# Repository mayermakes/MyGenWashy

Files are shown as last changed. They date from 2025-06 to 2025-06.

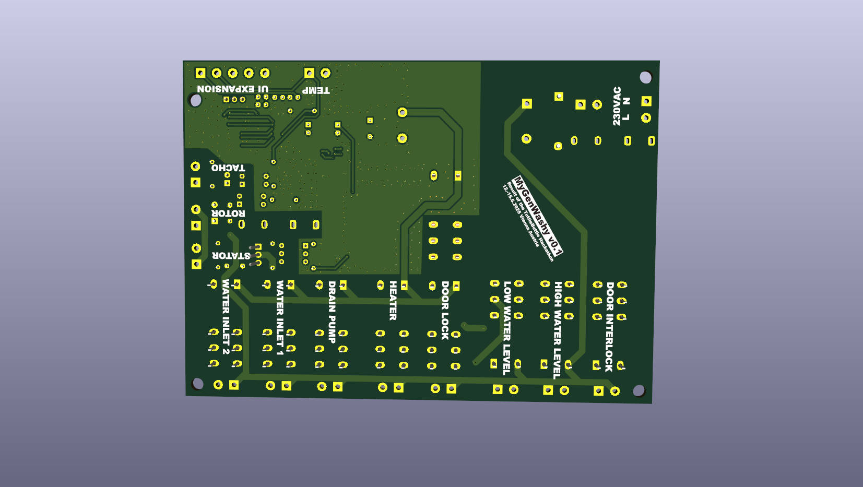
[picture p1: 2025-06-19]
mr_washi_back.png

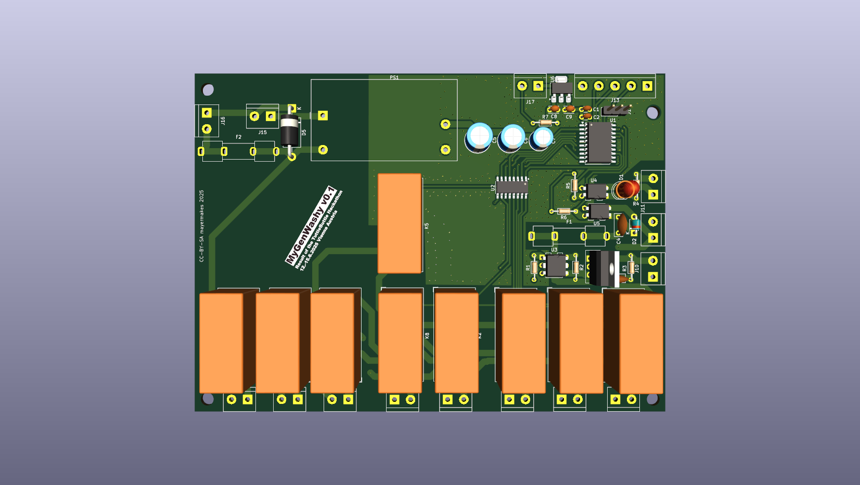
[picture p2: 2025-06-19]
mr_washi.png

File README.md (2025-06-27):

# MyGenWashy
Generic washing Machine Controller - Result of the TuttleButtle Hackathon 2025
held 13.-15.6.2025 in Vienna Austria.

the team got a broken washing machine and set the task to create a generic open source washing machine controler.
the original washing machine and its electronics and a chinese replacement board were partly reverse engineered to understand the functionality.
the team tested their theories on how safety mechanisms and machine parts worked and had to be controlled.
At the end of day two the machine was running a cold wash programm from a dev kit and some homemade electronics controlled via ESP-home.
On day three the learnings and circuits were converted into a kicad design for further testing and software development.

the board is intended to be locally produceable, by hand soldering and easy to repair. We avoided  "special" components for easy component substitution.
Unit cost is not a concerning factor, this is about the availability of a workable design that can be fitted with whatever components are available.

Thanks to Aisler for the Protoype PCBs and Farnell for supporting us with parts!

mr_washi_angled

mr_washi_back_angled

Find the Presentation PDF here:

[Hackathon EN-finial3.pdf](https://github.com/user-attachments/files/20941595/Hackathon.EN-finial3.pdf)

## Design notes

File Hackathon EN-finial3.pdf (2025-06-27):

# MyGenWashy: Modernizing Old

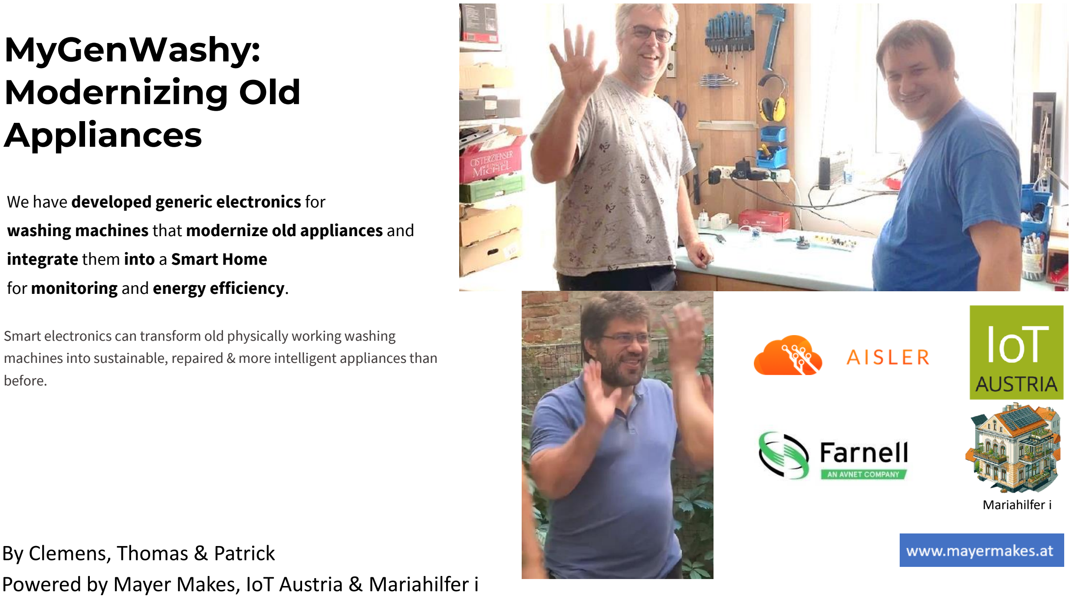
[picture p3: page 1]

# By Clemens, Thomas & Patrick Powered by Mayer Makes, IoT Austria & Mariahilfer i

# Appliances

# Smart electronics can transform old physically working washing machines into sustainable, repaired & more intelligent appliances than

before.

# We have developed generic electronics for

# washing machines that modernize old appliances and

# integrate them into a Smart Home

for monitoring and energy efficiency.

# Mariahilfer i

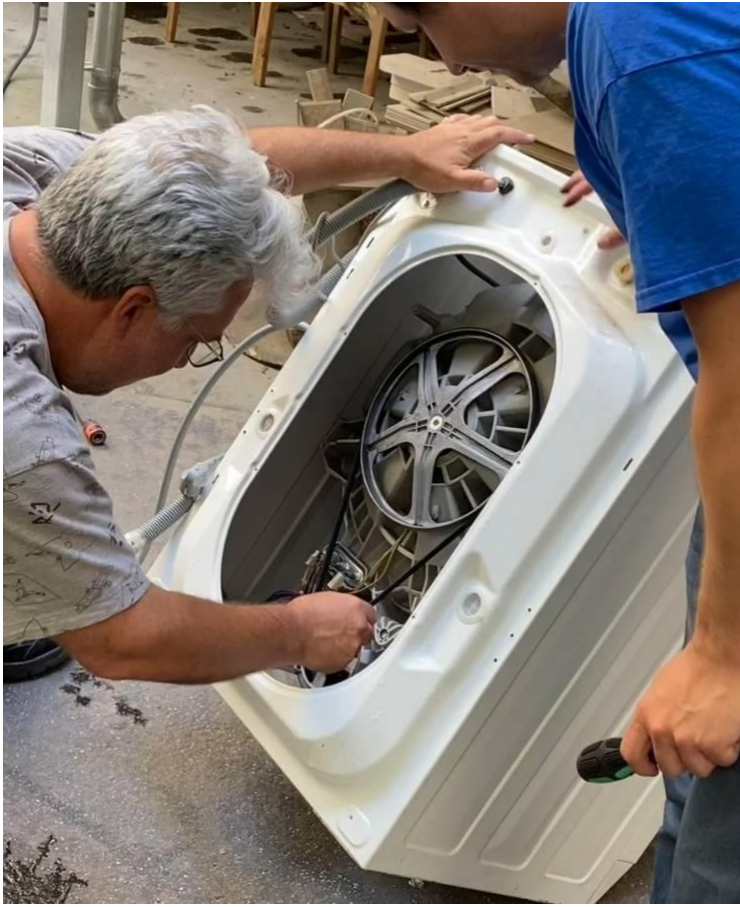
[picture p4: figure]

# Goal of the Hackathon

# Generic electronic components

# Development of a universal control system for washing machines

# Gain knowledge

# Understanding and documenting the components of a

# washing machine

# Smart Home Integration

# Connection to modern home automation systems

# Open Product Pass => http://odpp.at/ (July 2025)

# Create & customize digital documentation for CURRENT products

# Circular economy

# What have we learned?

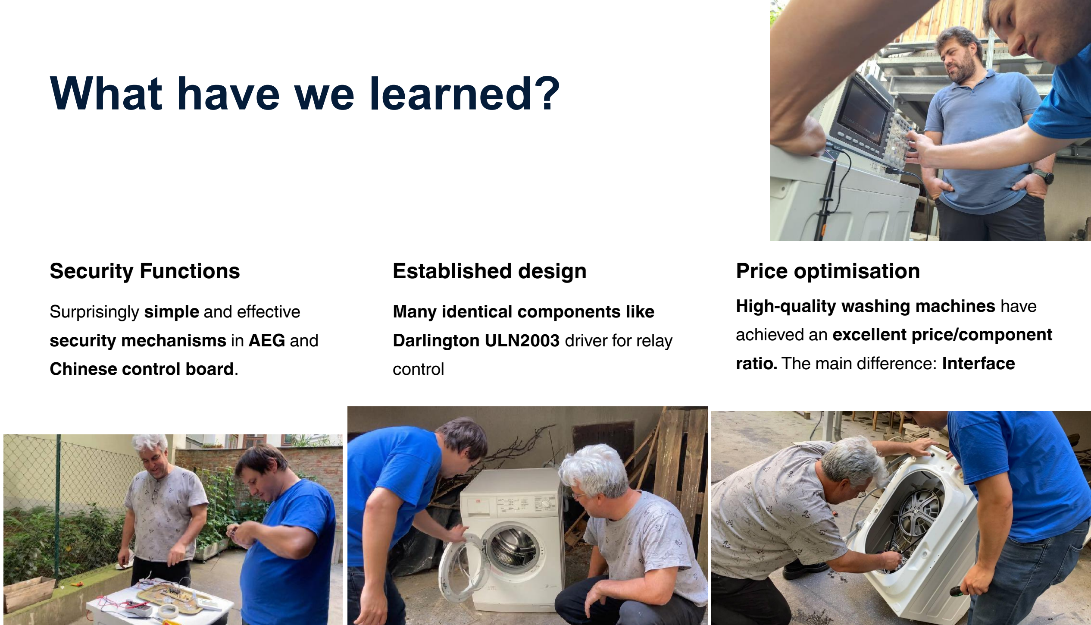
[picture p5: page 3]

# Security Functions

# Surprisingly simple and effective

# security mechanisms in AEG and

Chinese control board.

# Established design

# Many identical components like

# Darlington ULN2003 driver for relay

# control

# Price optimisation

# High-quality washing machines have

# achieved an excellent price/component

# ratio. The main difference: Interface

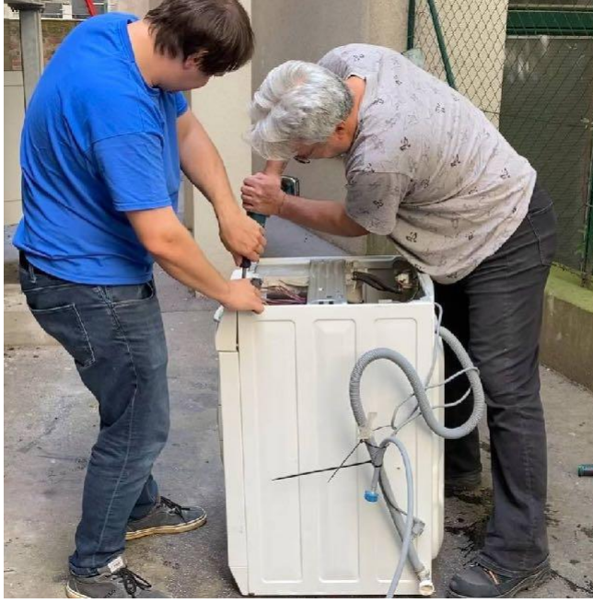
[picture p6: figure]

# Surprising discoveries

# Water level control – by air pressure !?

# Simple air membrane and air pressure => That was unexpected!

# Direct control

# 230V circuit without complex electronics => simplicity is King!

# Security system

Mechanical protection against overflow and overheating => Safety first – also on Chinese generic boards!

# Conclusions

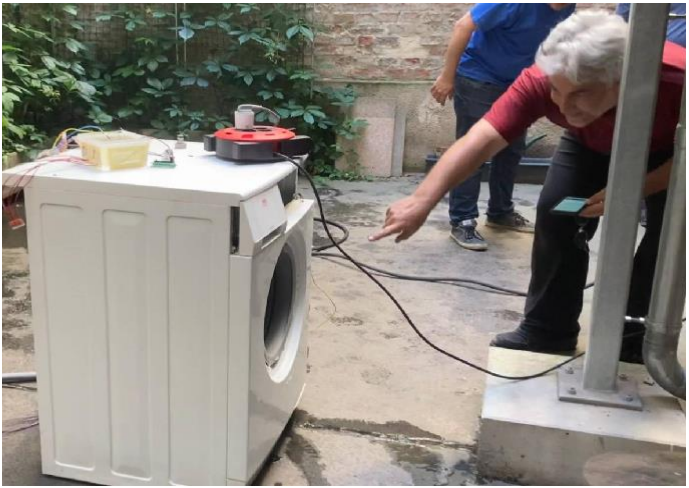
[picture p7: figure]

# Sophisticated technology

# The operating principle of a

# washing machine is fully

# developed and optimized

# Circular Economy

# High-quality machines can

# simply continue to be

# operated with new

# electronics. QED

# Sustainability: Refabrication, Pimp

# Replacing the electronics of an old washing machine with a

# generic one that has more energy-saving functions and is easier

# to control. This saves resources and reduces electronic waste!

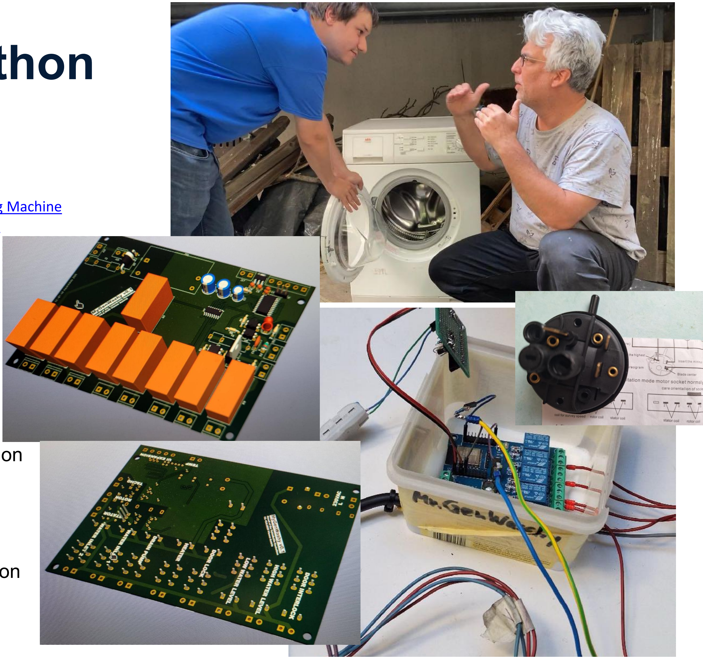
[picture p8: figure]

# Results of the Hackathon

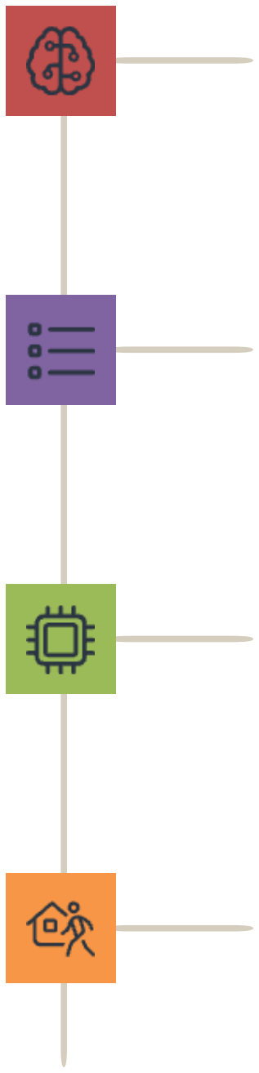
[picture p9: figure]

# Schematic for circuit v1/3

# Component list v1/3

# Complete component documentation

# Board v1/3

# PCB design for the MadWashyMax Edition

# Smart Home Integration

# GitHub - mayermakes/MyGenWashy: Generic washing Machine

Controller - Result of the TuttleButtle Hackathon 2025 (https://github.com/mayermakes/MyGenWashy)

# PCB design for the MadWashyMax Edition

# (intermediate Version here – will be

# updated once PCB Board v1 is here …)

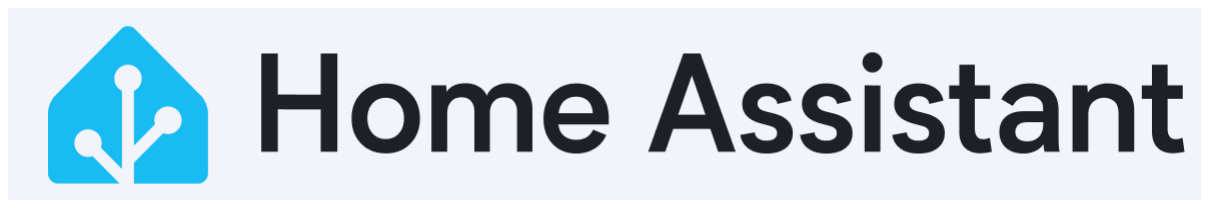
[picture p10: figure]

esphome:
name: mygenwashy-v2
friendly_name: MyGenWashy-v2

esp32:

board: esp32dev

framework:
type: arduino

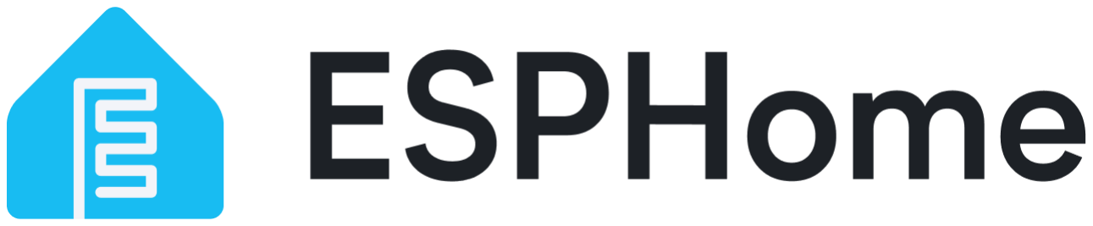
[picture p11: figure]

logger:
level: VERBOSE

output:
- platform: gpio

pin: GPIO32

id: relay_pin_1_relay_cold_water_valve
- platform: gpio

pin: GPIO33

id: relay_pin_2_relay_pump
- platform: gpio

pin: GPIO25

id: relay_pin_3_relay_montor_stator
- platform: gpio

pin: GPIO26

id: relay_pin_4_relay_montor_aktor
- platform: ledc #PWM Motor Speed

pin: GPIO27

frequency: 1000 Hz
id: pwm_motor

switch:

- platform: output
id: switch_relay_cold_water_valve

name: "R1 - Kaltwasserventil"

icon: mdi:Water
output: relay_pin_1_relay_cold_water_valve

restore_mode: RESTORE_DEFAULT_OFF

- platform: output
id: switch_relay_relay_pump

name: "R2 - Wasser abpumpen" icon: mdi:Pump
output: relay_pin_2_relay_pump
- platform: output
id: switch_relay_montor_stator name: "R3 - Motor Stator"
icon: mdi:Motor

output: relay_pin_3_relay_montor_stator

- platform: output
id: switch_relay_pin_4_relay_montor_aktor

name: "R4 - Motor Aktor"
icon: mdi:MotorAktor

output: relay_pin_4_relay_montor_aktor fan: #Washing Machine Rince Speed

- platform: speed
output: pwm_motor
name: "Motor Rotor Speed 3" icon: mdi:fan-speed-3
- platform: speed

output: pwm_motor
name: "Motor Stator Speed 2" icon: mdi:fan-speed-2

sensor:
- platform: ntc #NTC

sensor: resistance_sensor
calibration: #datasheet - or calkibrated - user instrcutions - MrWashyBalls #- 10.0kOhm -> 25°C

#- 27.219kOhm -> 0°C

#- 14.674kOhm -> 15°C

b_constant: 3950
reference_temperature: 25°C

reference_resistance: 10kOhm

name: "Water Temperature (NTC)" icon: mdi:thermometer-snowflake

- platform: resistance

id: resistance_sensor

sensor: source_sensor
configuration: DOWNSTREAM
resistor: 5 kOhm #Messen

name: Resistance Sensor

- platform: adc
id: source_sensor
pin: GPIO35

update_interval: 60s

- platform: gpio

pin:

number: GPIO34

mode: INPUT
inverted: false

name: "Umdrehungssignal"
filters:
- delayed_on: 10ms
- delayed_off: 10ms
icon: mdi:counter

# ESPHome & Home Assist

# ESPHome - Home Assistant (https://www.home-assistant.io/integrations/esphome)

# mygenwashy-v1.yaml

# remarks: Motor driver & NTC calibration will follow in

v2

# OnPrem Smart Home

# Post-apocalyptic SmartHome

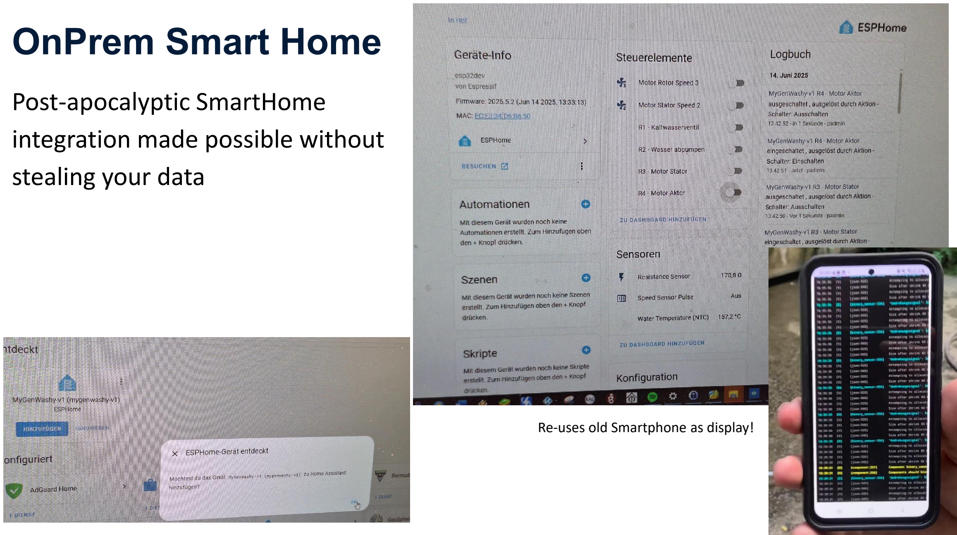
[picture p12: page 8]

# integration made possible without stealing your data

# Re-uses old Smartphone as display!

# Minimal Arch / i2c Bus / OnPrem Smart Home

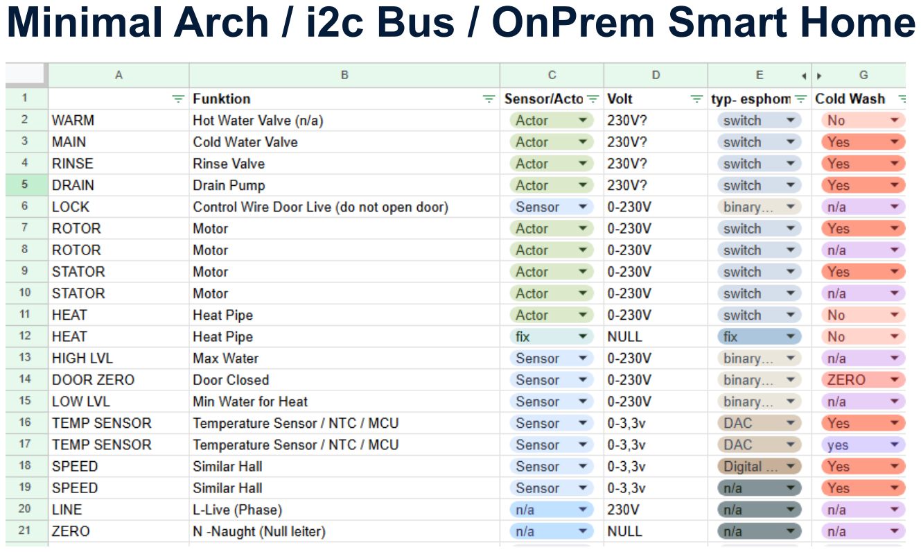
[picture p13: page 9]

# Modified MadWashyMax

# Hardware modification

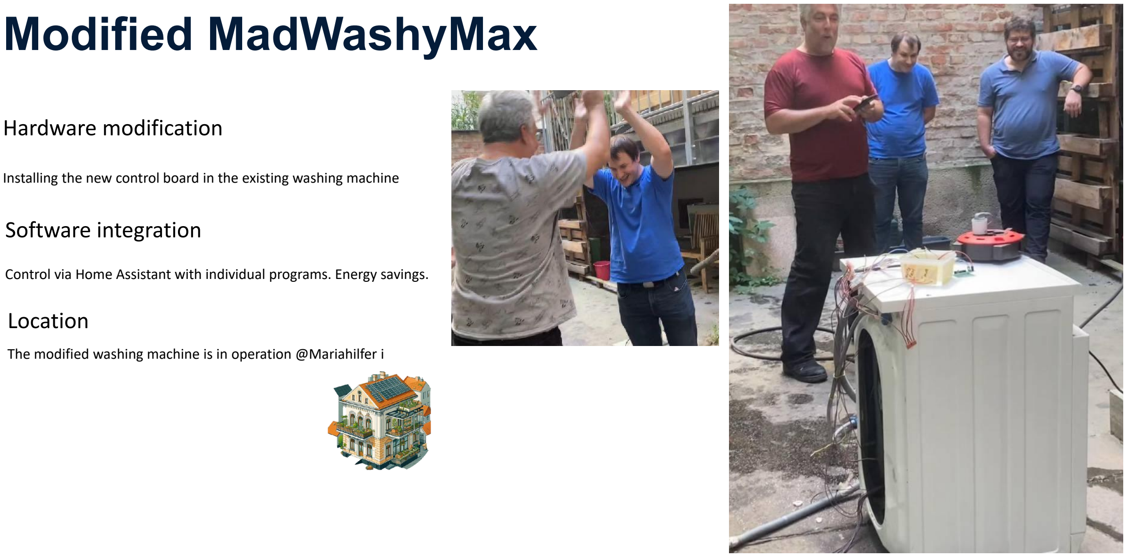
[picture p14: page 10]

# Installing the new control board in the existing washing machine

# Software integration

Control via Home Assistant with individual programs. Energy savings.

# Location

# The modified washing machine is in operation @Mariahilfer i

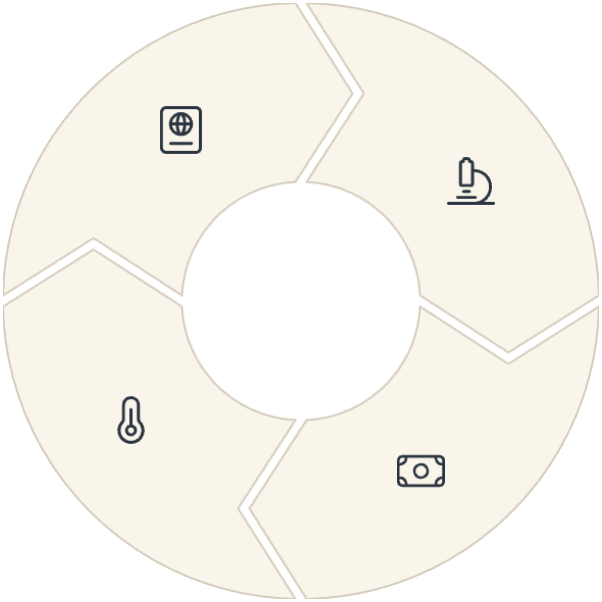
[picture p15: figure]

# Open Digital Product Pass – ODPP

# Examples of 4 household

# appliances incl. MadWashyMax =>

# in July check http://odpp.at/

# Washing quality monitoring

# StartUp idea for monitoring cleaning

# performance

# EnergyMate

# Control with dynamic electricity

# prices (StartUp)

# Energy-optimized water heating

# Real-time control for maximum

# efficiency

# Follow-Ups & Spin-Offs

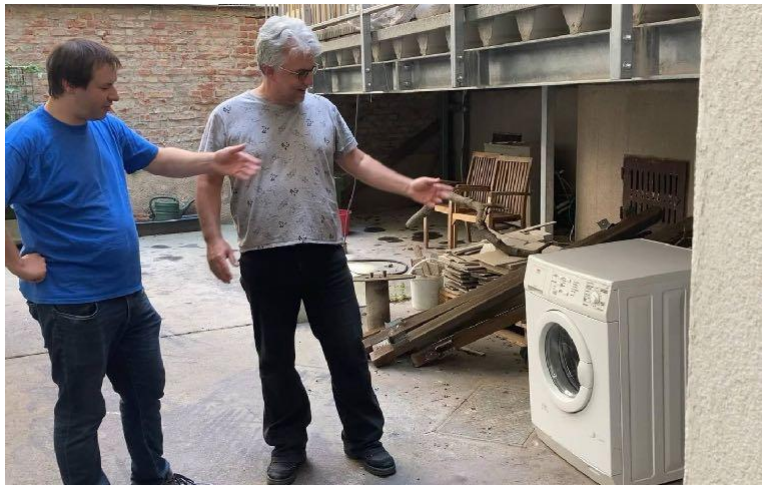
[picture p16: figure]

# Future vision

# Promoting sustainability

# Extend the service life of household appliances.Washing

machine => e-toothbrush => washing machine .... etc...

# Build a community => http://odpp.at/ (July)

Share knowledge and experiences.

# Driving innovation forward

# Develop new applications for existing technology. Which can be

# used TODAY by anyone!

# Our project shows how we can use open source technology to

# reduce e-waste and create new business models at the same time

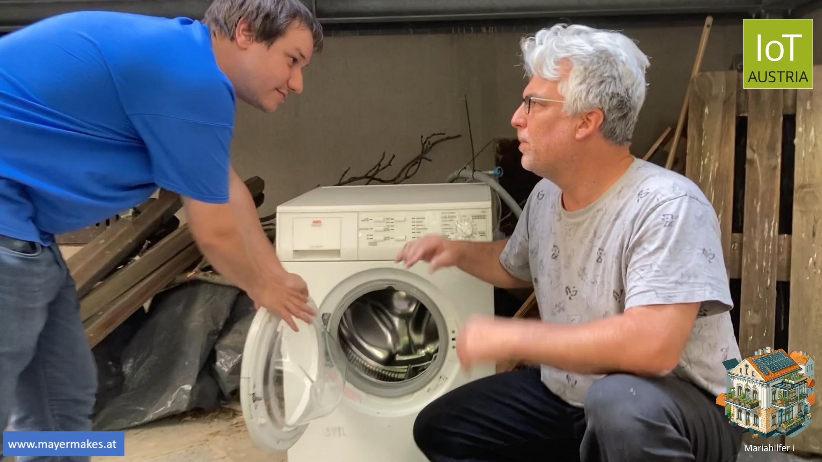
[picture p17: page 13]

# Mariahilfer i

# Tadaaa!

# Water

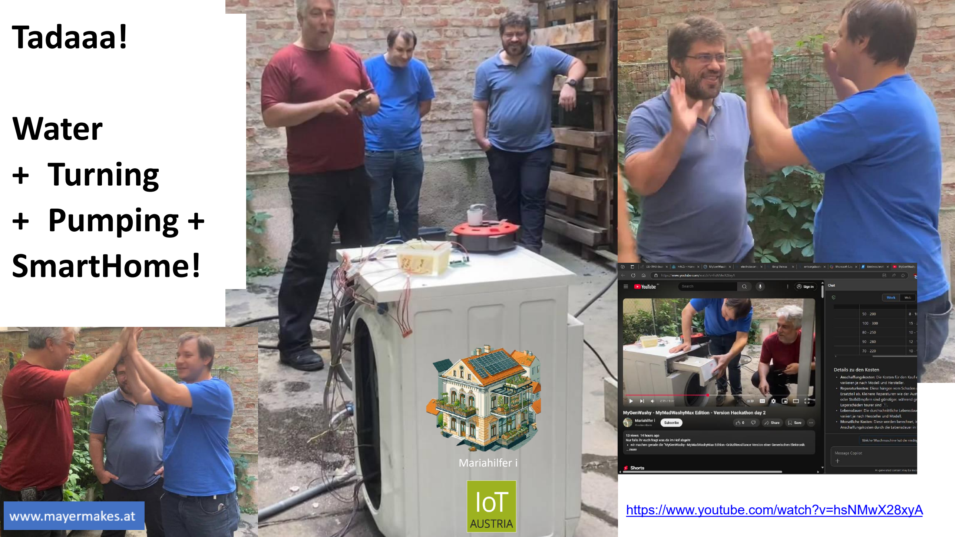
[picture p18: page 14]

# + Turning + Pumping + SmartHome!

# https://www.youtube.com/watch?v=hsNMwX28xyA

# Mariahilfer i

# Clemens Mayer

MAYER MAKES e.U.

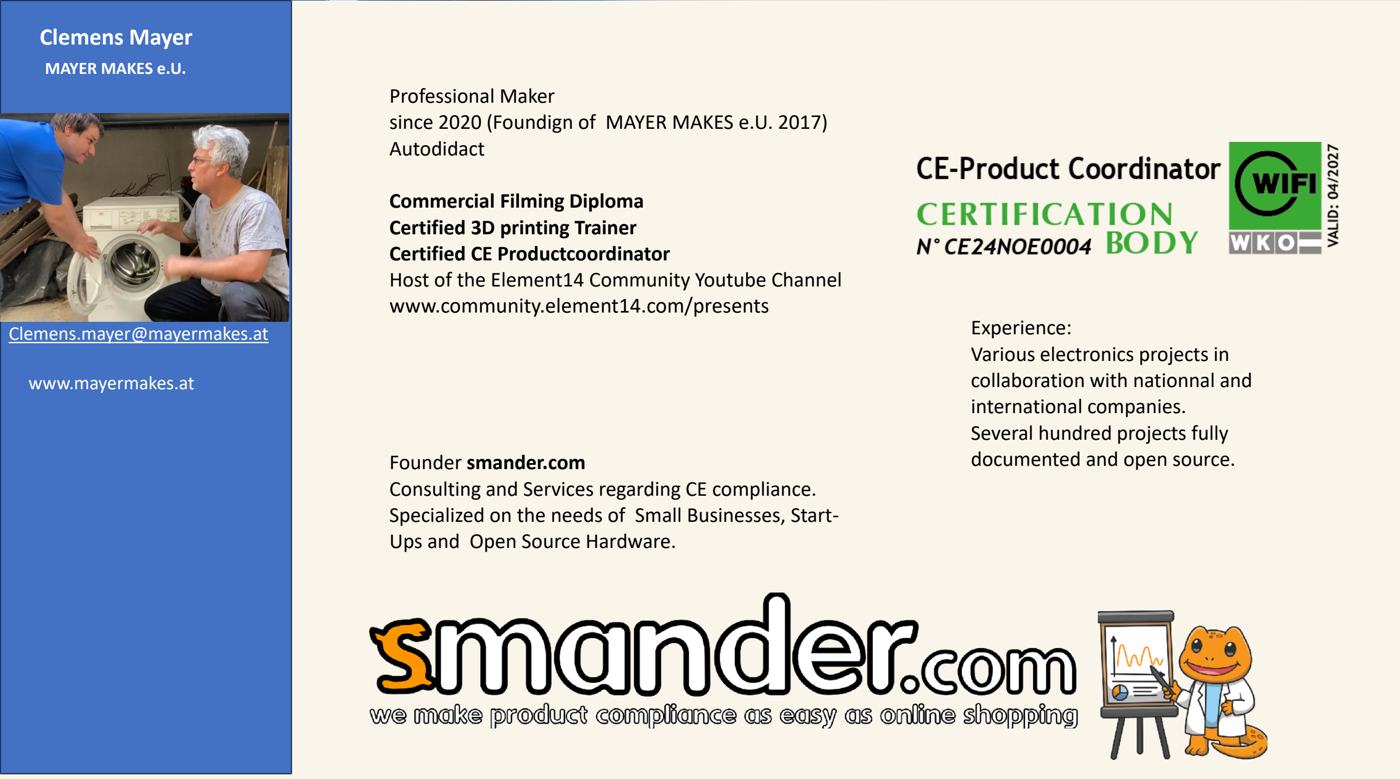
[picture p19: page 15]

# Clemens.mayer@mayermakes.at

# www.mayermakes.at

# Professional Maker since 2020 (Foundign of MAYER MAKES e.U. 2017) Autodidact

# Commercial Filming Diploma Certified 3D printing Trainer Certified CE Productcoordinator Host of the Element14 Community Youtube Channel

# www.community.element14.com/presents

# Founder smander.com

Consulting and Services regarding CE compliance.

# Specialized on the needs of Small Businesses, Start-

Ups and Open Source Hardware.

# Experience: Various electronics projects in collaboration with nationnal and

international companies.

# Several hundred projects fully

documented and open source.

DI Patrick Ch. AWART | Ausbildung:
| • Master TU Wien / Technische Informatik 2001 • Data Science / Hopkins Universität 2017

# Kernkompetenzen:

# - Innovation Lead / Guide for Digital Transformation - KI Experte & Data Scientist - Wissensmanagement - Complex System Assessment / Evaluation

# - AI Roadmap & Strategiefindung

- Smart Product Use Case Entwicklung, Bewertung,

# Spezifizierung und Umsetzungsverantwortung

# - Python / Node js / IoT / … / (No-)SQL / Elastic Stack / diverse Programmier & Abfragesprachen von C über

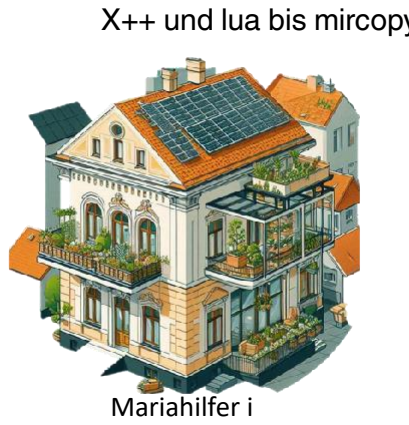
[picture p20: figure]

X++ und lua bis mircopython der letzten 35 Jahre.

# Fortbildung, Kurse & Zertifizierungen:

# - Google Advanced AI Solutions 2019

# - Azure ML 2018

# - Scrum Master 2018

# - Zertifizierter Innovationsmanager 2008

# - Microsoft Certified Professional 2013

# Projekte / Erfahrung:

# Maßgebliche fachliche Leitung von Digitalen

Transformationsprojekten in den Branchen SmartCity,

# eGoverment, Public Health & Krisenmanagement Systeme -

seit 25 Jahren.

# Principal Solution Architect

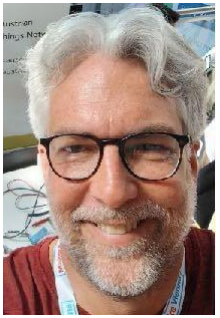
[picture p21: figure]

# p@awart.net

+43 664 88 55 13 77

# Sprachen: D, E, F

# stolzer Vater von 2 Kindern (Bea hat mit 4

# Jahren löten gelernt)

# Hobby: Hiking/Volleyball/ MTB

# Kreislaufwirtschaftliche Entwicklung im

# Bestand Energiegemeinschaften &

# Lastprofil-optimierung

# Co-Gründer Mariahilfer i Nov 2024 360°

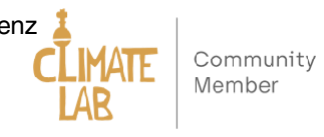
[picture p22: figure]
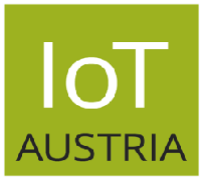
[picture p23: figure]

# Gräzl-Resilienz

# - Von der Vision über die Prozess- & Anforderungsanalyse bis hin zum Go Live

# - Strategieentwicklung und Umsetzung

# - DPP / Digitaler Produktpass - ODPP / Offener DPP

# - Kintsugi Repair Cafe - (u.a.Wohn Interieur)

# - KI-Wissensmanagement Mariahilfer i

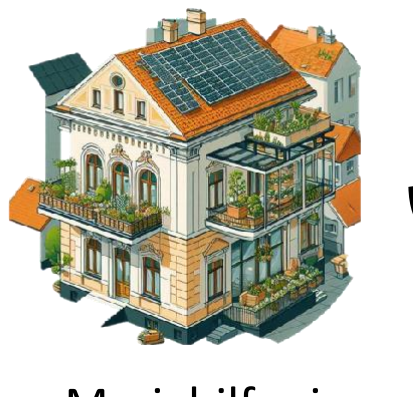
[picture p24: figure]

# JOIN US for v2, v3 & StartUps!

# Get in touch and participate in our future projects advancing open source and reusability

# Patrick Awart

# Thomas Losert

# Clemens Mayer

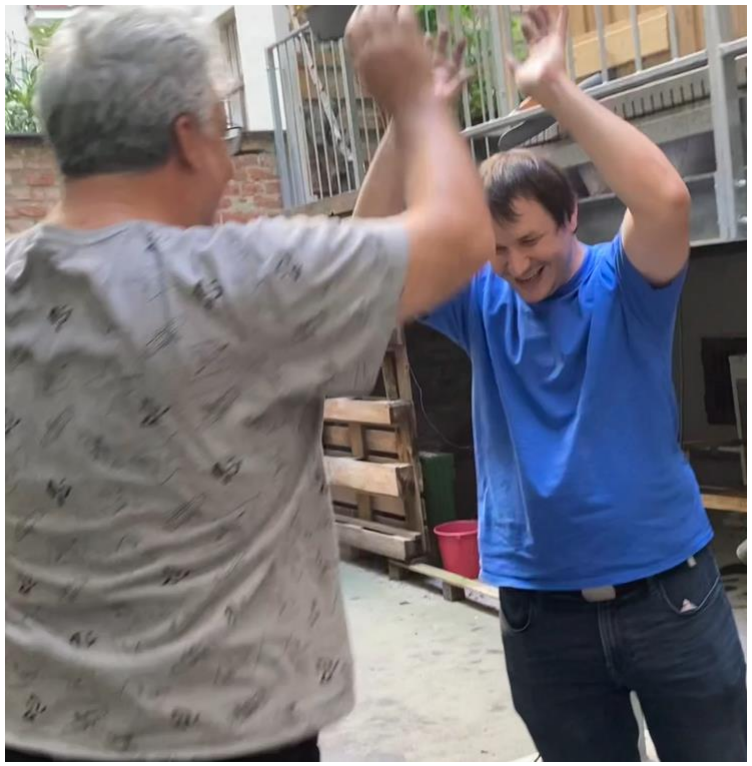
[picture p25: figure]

# Open Digital Product Pass => http://odpp.at/ (July 2025) contribute@odpp.at

# Mariahilfer i

# MANY Thx go to:

Albert (pixs, Transport, Vids, PPT !), Johanna (Washing machine!), Birgit (UX Feedback & Requirements Feedback),

Boots Owen (Many Many Useful tips!!!) check out: https://youtu.be/f2Fo3-SVfDs Farnell – components Aisler – PC Board Infineon – AI Boards Gorenje – CircThread Inspiration for ODPP! D. (crimping!) Kintsugi Repair Café (Space!) CargoBike! Gemma, CoPilot, etc. Cool AI Pictures raising the Adrenalin Levels! Elektra and Nescafe Coffee machine RuSZ: David & Dagmar – Aligning Elektro Kuchling: Feedback of current sales practice & Inspiration on ReUse Ideas Generic (!!!) Water Adapter from WaterFront lying around – you saved us! !!! Let's keep up the great Work & Vibes!!!

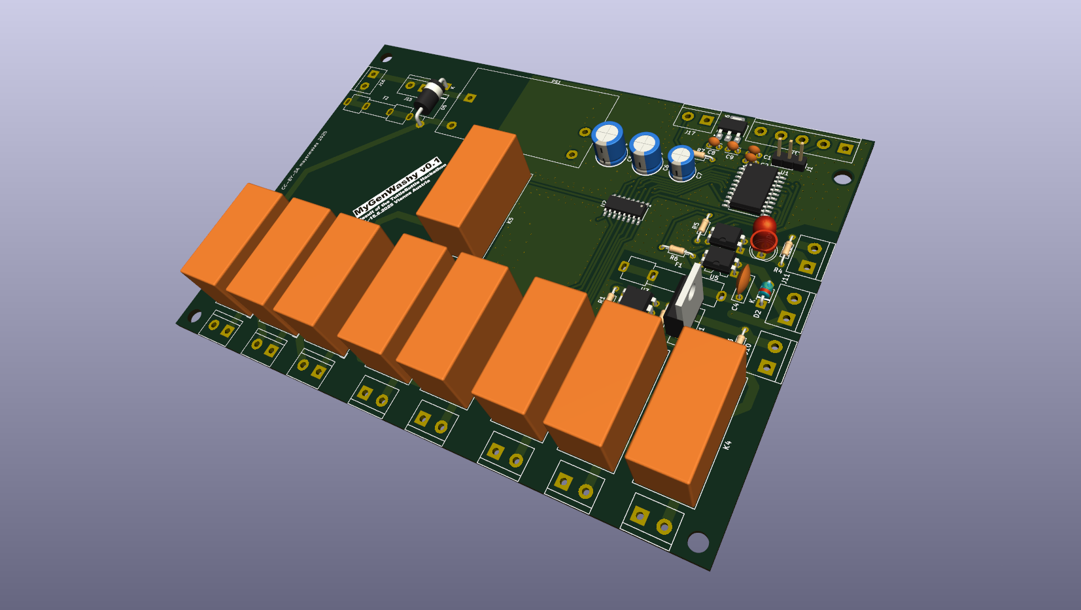
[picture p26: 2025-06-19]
mr_washi_angled.png

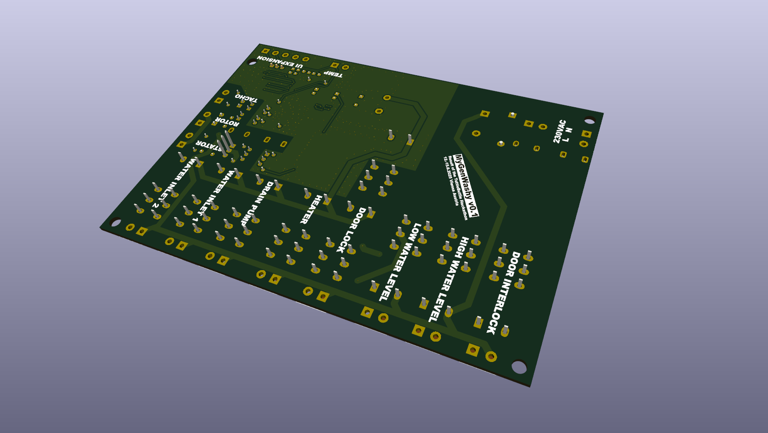
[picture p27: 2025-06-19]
mr_washi_back_angled.png

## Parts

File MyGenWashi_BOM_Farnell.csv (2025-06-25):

Nr. | Best.-Nr. | RoHS-konform? | Ihre Bestellnummer | Hinweise | Menge | Hersteller-Teilenr. | Herstellername | Hersteller / Beschreibung | Verfügbarkeit | Stückpreis (&euro;) | Positionspreis (&euro;) | Rabattpreis (&euro;)
1 | 3765485 | RoHS: YES / PHTHALATE: YES |  |  | 6.0 | PS2562L1-1-A | RENESAS | RENESAS Optokoppler, 1 Kanal, DIP, Oberflächenmontage, 4 Pin(s), 80 mA, 5 kV, 200 % | 671 | 0.9710 | 5.83
2 | 8767068 | RoHS: YES / PHTHALATE: YES |  |  | 5.0 | ECA1AAM331X | PANASONIC | PANASONIC Elektrolytkondensator, 330 µF, 10 V, ± 20%, Radial bedrahtet, 2000 Stunden bei 85°C, Polarisiert | 1905 | 0.1130 | 0.57
3 | 1459143 | RoHS: Y-EX / PHTHALATE: YES |  |  | 5.0 | MUR2100EG | ONSEMI | ONSEMI Diode mit kurzer/ultrakurzer Erholzeit, 1 kV, 2 A, Einfach, 2.2 V, 75 ns, 35 A | 6522 | 0.4570 | 2.29
4 | 3406865 | RoHS: YES / PHTHALATE: YES |  |  | 10.0 | RTD14730 | SCHRACK - TE CONNECTIVITY | SCHRACK - TE CONNECTIVITY Leistungsrelais, SPDT, 230 VAC, 16 A, RT1, Durchsteckmontage, Monostabil | 532 | 6.5700 | 65.70
5 | 3705262 | RoHS: YES / PHTHALATE: YES |  |  | 40.0 | 1755736 | PHOENIX CONTACT | PHOENIX CONTACT STIFTLEISTE, VERT 5.08MM 2POL. | 3030 | 0.9610 | 38.44
6 | 3705389 | RoHS: Y-EX / PHTHALATE: YES |  |  | 2.0 | 1757048 | PHOENIX CONTACT | PHOENIX CONTACT Steckbare Reihenklemme, 5.08 mm, 5 -polig, 24 AWG, 12 AWG, 2.5 mm², Schraubanschluss | 1234 | 5.7600 | 11.52
7 | 3705201 | RoHS: YES / PHTHALATE: YES |  |  | 2.0 | 1757271 | PHOENIX CONTACT | PHOENIX CONTACT Reihenklemme, abgewinkelt, Stiftleiste, 5.08 mm, 5 -polig, 12 A, 250 V | 1065 | 1.8900 | 3.78
8 | 1581137 | RoHS: YES / PHTHALATE: YES |  |  | 5.0 | MCL053MD | MULTICOMP PRO | MULTICOMP PRO LED, Rot, Durchsteckmontage, T-1 3/4 (5mm), 20 mA, 2 V, 625 nm | 34709 | 0.1260 | 0.63
9 | 3772379 | RoHS: YES / PHTHALATE: YES |  |  | 10.0 | FG18X5R1E106MRT00 | TDK | TDK Keramikvielschichtkondensator, 10 µF, 25 V, ± 20%, PC-Pin, X5R, 2.5 mm | 489 | 0.2650 | 2.65
10 | 3289391 | RoHS: YES / PHTHALATE: YES |  |  | 10.0 | K104Z15Y5VE5TH5 | VISHAY | VISHAY Keramikvielschichtkondensator, 0.1 µF, 25 V, -20%, +80%, Radial bedrahtet, Y5V, 5 mm | 294 Verfügbar | bis der Lagerbestand erschöpft ist. | 0.1060 | 1.06
11 | 4143903 | RoHS: YES / PHTHALATE: YES |  |  | 5.0 | FG23C0G2W104JNT00 | TDK | TDK Keramikvielschichtkondensator, 0.1 µF, 450 V, ± 5%, PC-Pin, C0G / NP0, 5 mm | 386 | 3.0000 | 15.00
12 | 2534925 | RoHS: YES / PHTHALATE: YES |  |  | 10.0 | C981U103MYVDAAWL45 | KEMET | KEMET Funkentstörkondensator (Keramik), Scheibenkondensator, 0.01 µF, ± 20%, X1 / Y2, 400 V, 250 V | 5900 Verfügbar | bis der Lagerbestand erschöpft ist. | 0.3340 | 3.34
13 | 1471017 | RoHS: YES / PHTHALATE: YES |  |  | 3.0 | MOC3020-M | ONSEMI | ONSEMI Optokoppler, Triac-Ausgang, DIP, 6 Pin(s), 5.3 kV, Momentwert, 400 V, MOC301XM & MOC302XM | 4446 | 0.7160 | 2.15
14 | 1578404 | RoHS: YES / PHTHALATE: YES |  |  | 5.0 | MCP1825S-3302E/DB | MICROCHIP | MICROCHIP LDO-Festspannungsregler, 2.1V bis 6V, 210mV Dropout, 3.3Vout, 500mAout, SOT-223-3 | 50652 | 0.6290 | 3.15
15 | 1653491 | RoHS: YES / PHTHALATE: YES |  |  | 4.0 | BTB16-600BWRG | STMICROELECTRONICS | STMICROELECTRONICS Triac, 600 V, 16 A, TO-220AB, 1.3 V, 160 A, 50 mA | 1236 | 1.2800 | 5.12
16 | 3619410 | RoHS: YES / PHTHALATE: YES |  |  | 5.0 | MP006456 | MULTICOMP PRO | MULTICOMP PRO Widerstand für Durchsteckmontage, 47 kohm, 1 W, ± 2%, Axial bedrahtet, 500 V | 1545 | 0.2590 | 1.30
17 | 2815498 | RoHS: YES / PHTHALATE: YES |  |  | 2.0 | IRM-10-5 | MEAN WELL | MEAN WELL AC/DC-Netzteil für Leiterplattenmontage, ITE, 1 Ausgang, 10 W, 5 VDC, 2 A | 64 | 10.7400 | 21.48
18 | 2325629 | RoHS: YES / PHTHALATE: YES |  |  | 20.0 | 1-1415899-9 | SCHRACK - TE CONNECTIVITY | SCHRACK - TE CONNECTIVITY Universelles Leistungsrelais, Baureihe RZ, monostabil, SPDT, 5V DC, 16A | 3485 | 1.8600 | 37.20
19 | 1217315 | RoHS: YES / PHTHALATE: YES |  |  | 40.0 | MC 100-50802 | LUMBERG | LUMBERG Steckbare Reihenklemme, 5.08 mm, 2 -polig, 24 AWG, 14 AWG, Schraubanschluss | 1780 Verfügbar | bis der Lagerbestand erschöpft ist. | 0.9440 | 37.76
20 | 9452192 | RoHS: YES / PHTHALATE: YES |  |  | 5.0 | MCUMR16V106M4X5 | MULTICOMP PRO | MULTICOMP PRO Elektrolytkondensator, 10 µF, 16 V, ± 20%, Radial bedrahtet, 1000 Stunden bei 85°C, Polarisiert | 68408 | 0.1040 | 0.52
21 | 1902919 | RoHS: YES / PHTHALATE: YES |  |  | 5.0 | MCRH50V104M5X11 | MULTICOMP PRO | MULTICOMP PRO Elektrolytkondensator, 0.1 µF, 50 V, ± 20%, Radial bedrahtet, 2000 Stunden bei 105°C, Polarisiert | 302 | 0.0788 | 0.39
22 | 9338055 | RoHS: YES / PHTHALATE: YES |  |  | 5.0 | MCF 2W 1K | MULTICOMP PRO | MULTICOMP PRO KOHLESCHICHTWIDERSTAND 1K 5% 2W AXIAL | 95811 | 0.1540 | 0.77
23 | 9338705 | RoHS: YES / PHTHALATE: YES |  |  | 5.0 | MCF 0.5W 330R | MULTICOMP PRO | MULTICOMP PRO Widerstand für Durchsteckmontage, 330 ohm, MCF Series, 500 mW, ± 5%, Axial bedrahtet, 350 V | 10903 | 0.0727 | 0.36
24 | 4227313 | RoHS: YES / PHTHALATE: YES |  |  | 5.0 | MCPKNPA1WJ0101A10 | MULTICOMP PRO | MULTICOMP PRO Widerstand für Durchsteckmontage, 100 ohm, MCPKNPA Series, 1 W, ± 5%, Axial bedrahtet, 500 V | 1888 | 0.2540 | 1.27
25 | 1357917 | RoHS: YES / PHTHALATE: YES |  |  | 5.0 | MOR03SJ0103A19 | MULTICOMP PRO | MULTICOMP PRO METALLOXIDWIDERSTAND, 10K, 5%, 3W, AXIAL | 3295 | 0.2780 | 1.39
26 | 9343318 | RoHS: YES / PHTHALATE: YES |  |  | 5.0 | MF12 5K1 | MULTICOMP PRO | MULTICOMP PRO Widerstand für Durchsteckmontage, 5.1 kohm, MF12 Series, 125 mW, ± 1%, Axial bedrahtet, 200 V | 4729 | 0.0614 | 0.31
27 | 3872794 | RoHS: YES / PHTHALATE: YES |  |  | 5.0 | ATTINY3226-SU | MICROCHIP | MICROCHIP 8-Bit-MCU, tinyAVR 2 Family ATtiny3226 Series Microcontrollers, AVR, 20 MHz, 32 KB, 20 Pin(s) | 423 | 1.2500 | 6.25
28 | 2628016 | RoHS: YES / PHTHALATE: YES |  |  | 5.0 | ULN2003ADR2G | ONSEMI | ONSEMI DARLINGTON-TRANSISTOR-ARRAY, SOIC-16 | 5532 | 1.0300 | 5.15
29 | 2677537 | RoHS: YES / PHTHALATE: YES |  |  | 5.0 | 1.5KE400CA | TAIWAN SEMICONDUCTOR | TAIWAN SEMICONDUCTOR TVS-Diode, 1.5KE, Bidirektional, 342 V, 548 V, DO-201AE, 2 Pin(s) | 187 | 0.7920 | 3.96
 |  |  |  |  |  |  | Zwischensumme | &euro;279.32
 |  |  |  |  |  |  | Warengesamtsumme | &euro;279.32
 |  |  |  |  |  |  | Lieferung | &euro;0.00
 |  |  |  |  |  |  | USt. | &euro;55.86
 |  |  |  |  |  |  | Gesamt | &euro;335.18

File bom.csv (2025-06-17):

Reference | Value | Datasheet | Footprint | Qty | DNP
C1,C6,C8,C9 | 10uF | ~ | -- verschiedene Werte -- | 4
C2,C7 | 0,1uF | ~ | -- verschiedene Werte -- | 2
C3 | 400V 100nF | ~ | Capacitor_THT:C_Disc_D7.0mm_W2.5mm_P5.00mm | 1
C4 | 400V 10nF | ~ | Capacitor_THT:C_Disc_D7.0mm_W2.5mm_P5.00mm | 1
C5 | 330uF | ~ | Capacitor_THT:CP_Radial_D8.0mm_P5.00mm | 1
D1 | LED | ~ | LED_THT:LED_D5.0mm | 1
D2 | D | ~ | Diode_THT:D_T-1_P5.08mm_Horizontal | 1
D5 | 1.5KExxCA | https://www.vishay.com/docs/88301/15ke.pdf | Diode_THT:D_DO-201AE_P15.24mm_Horizontal | 1
F1 | 100mA | ~ | Fuse:Fuseholder_Clip-5x20mm_Keystone_3512_Inline_P23.62x7.27mm_D1.02x1.57mm_Horizontal | 1
F2 | Fuse | ~ | Fuse:Fuseholder_Clip-5x20mm_Keystone_3512_Inline_P23.62x7.27mm_D1.02x1.57mm_Horizontal | 1
J1 | PRG_01x03_Pin | ~ | Connector_PinHeader_2.54mm:PinHeader_1x03_P2.54mm_Vertical | 1
J2 | DRAIN PUMP | ~ | TerminalBlock:TerminalBlock_bornier-2_P5.08mm | 1
J3 | HEATER | ~ | TerminalBlock:TerminalBlock_bornier-2_P5.08mm | 1
J4 | WATER INLET 1 | ~ | TerminalBlock:TerminalBlock_bornier-2_P5.08mm | 1
J5 | WATER INLET 2 | ~ | TerminalBlock:TerminalBlock_bornier-2_P5.08mm | 1
J6 | LOW_LEVEL | ~ | TerminalBlock:TerminalBlock_bornier-2_P5.08mm | 1
J7 | HIGH_LEVEL | ~ | TerminalBlock:TerminalBlock_bornier-2_P5.08mm | 1
J8 | DOOR LOCK | ~ | TerminalBlock:TerminalBlock_bornier-2_P5.08mm | 1
J9 | DOOR_INTERLOCK | ~ | TerminalBlock:TerminalBlock_bornier-2_P5.08mm | 1
J10 | STATOR | ~ | TerminalBlock:TerminalBlock_bornier-2_P5.08mm | 1
J11 | ROTOR | ~ | TerminalBlock:TerminalBlock_bornier-2_P5.08mm | 1
J12 | TACHO | ~ | TerminalBlock:TerminalBlock_bornier-2_P5.08mm | 1
J13 | Conn_01x05_Socket | ~ | TerminalBlock:TerminalBlock_bornier-5_P5.08mm | 1
J15 | Conn_01x02_Socket | ~ | TerminalBlock:TerminalBlock_bornier-2_P5.08mm | 1
J16 | 230V_IN | ~ | TerminalBlock:TerminalBlock_bornier-2_P5.08mm | 1
J17 | NTC 5k | ~ | TerminalBlock:TerminalBlock_bornier-2_P5.08mm | 1
K1,K2,K3,K4,K5,K8 | RZ03-1C4-D005 | https://www.te.com/commerce/DocumentDelivery/DDEController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 | Relay_THT:Relay_SPDT_Schrack-RT1-16A-FormC_RM5mm | 6
K6,K7,K9 | RTD14730 | https://www.te.com/commerce/DocumentDelivery/DDEController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 | Relay_THT:Relay_SPDT_Schrack-RT1-16A-FormC_RM5mm | 3
PS1 | IRM-10-5 | https://www.meanwell.com/Upload/PDF/IRM-10/IRM-10-SPEC.PDF | Converter_ACDC:Converter_ACDC_MeanWell_IRM-10-xx_THT | 1
Q1 | BTB16-600B | https://www.st.com/resource/en/datasheet/bta16.pdf | Package_TO_SOT_THT:TO-220-3_Vertical | 1
R1 | 1k | ~ | Resistor_THT:R_Axial_DIN0204_L3.6mm_D1.6mm_P7.62mm_Horizontal | 1
R2 | 330 | ~ | Resistor_THT:R_Axial_DIN0204_L3.6mm_D1.6mm_P7.62mm_Horizontal | 1
R3 | 100 | ~ | Resistor_THT:R_Axial_DIN0204_L3.6mm_D1.6mm_P7.62mm_Horizontal | 1
R4 | 10k | ~ | Resistor_THT:R_Axial_DIN0204_L3.6mm_D1.6mm_P7.62mm_Horizontal | 1
R5,R6 | 47k | ~ | Resistor_THT:R_Axial_DIN0204_L3.6mm_D1.6mm_P7.62mm_Horizontal | 2
R7 | 5k | ~ | Resistor_THT:R_Axial_DIN0204_L3.6mm_D1.6mm_P7.62mm_Horizontal | 1
U1 | ATtiny3226-S | https://ww1.microchip.com/downloads/en/DeviceDoc/ATtiny3224-3226-3227-Data-Sheet-DS40002345A.pdf | Package_SO:SOIC-20W_7.5x12.8mm_P1.27mm | 1
U2 | ULN2003 | http://www.ti.com/lit/ds/symlink/uln2003a.pdf | Package_SO:SOIC-16_3.9x9.9mm_P1.27mm | 1
U3 | MOC3020M | https://www.onsemi.com/pub/Collateral/MOC3023M-D.PDF | Package_DIP:DIP-6_W7.62mm | 1
U4,U5 | PC817 | http://www.soselectronic.cz/a_info/resource/d/pc817.pdf | Package_DIP:DIP-4_W7.62mm | 2
U6 | MCP1825S | http://ww1.microchip.com/downloads/en/devicedoc/22056b.pdf | Package_TO_SOT_SMD:SOT-223-3_TabPin2 | 1

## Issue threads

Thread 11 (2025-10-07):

j13 - UI Expantion - add sepc name and pinout

imariahilfer-svg, 2025-10-07:
j13 UI Expantion - add sepc name and pinout, cange numvering (?)

5 GND (OK)
4 SDA
3 SCL
2 3,3V
1 5V [Eckig, in Ecke] (OK)

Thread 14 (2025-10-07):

describe first flash of attiny with arduiono ide

imariahilfer-svg, 2025-10-07:
ATIny3226s

Arduiono: libary für board:
http://drazzy.com/package_drazzy.com_index.json
install ATTiny core >1.5.2

imariahilfer-svg, 2025-10-07:
see / reference / reuse: https://www.instructables.com/Install-ATTINY-Core-on-Arduino-232-Windows-10-64bi/

imariahilfer-svg, 2025-10-07:
or is it all alreday installed * confuzzed* Tool
arduino:avr-gcc@7.3.0-atmel3.6.1-arduino7 already installed
Downloading packages
arduino:avrdude@6.3.0-arduino18
ATTinyCore:micronucleus@2.5-azd1b
Failed to install platform: 'ATTinyCore:avr:1.5.2'.
Error: 2 UNKNOWN:

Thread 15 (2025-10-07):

Distance C8/C)

Black-Series-63, 2025-10-07:
C8 and C9 are too close together. The housings are touching

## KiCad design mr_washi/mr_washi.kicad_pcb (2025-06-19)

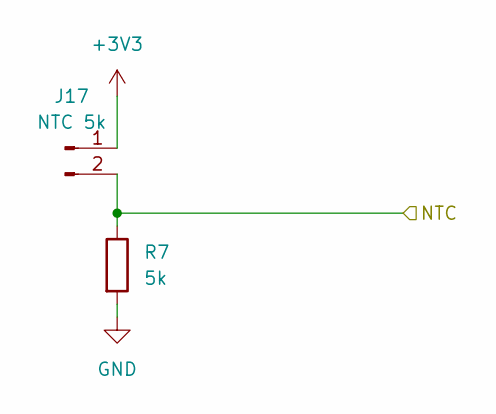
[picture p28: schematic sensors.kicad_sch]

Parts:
J17: NTC 5k; TerminalBlock_bornier-2_P5.08mm
R7: 5k; R_Axial_DIN0204_L3.6mm_D1.6mm_P7.62mm_Horizontal

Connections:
+3V3: J17.1; also elsewhere on the board
/MCU/7: J17.2, R7.1; also elsewhere on the board
GND: R7.2; also elsewhere on the board

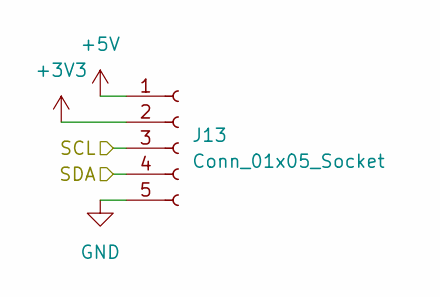
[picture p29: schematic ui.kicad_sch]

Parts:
J13: Conn_01x05_Socket; TerminalBlock_bornier-5_P5.08mm

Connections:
+3V3: J13.2; also elsewhere on the board
+5V: J13.1; also elsewhere on the board
/MCU/8: J13.4; also elsewhere on the board
/MCU/9: J13.3; also elsewhere on the board
GND: J13.5; also elsewhere on the board

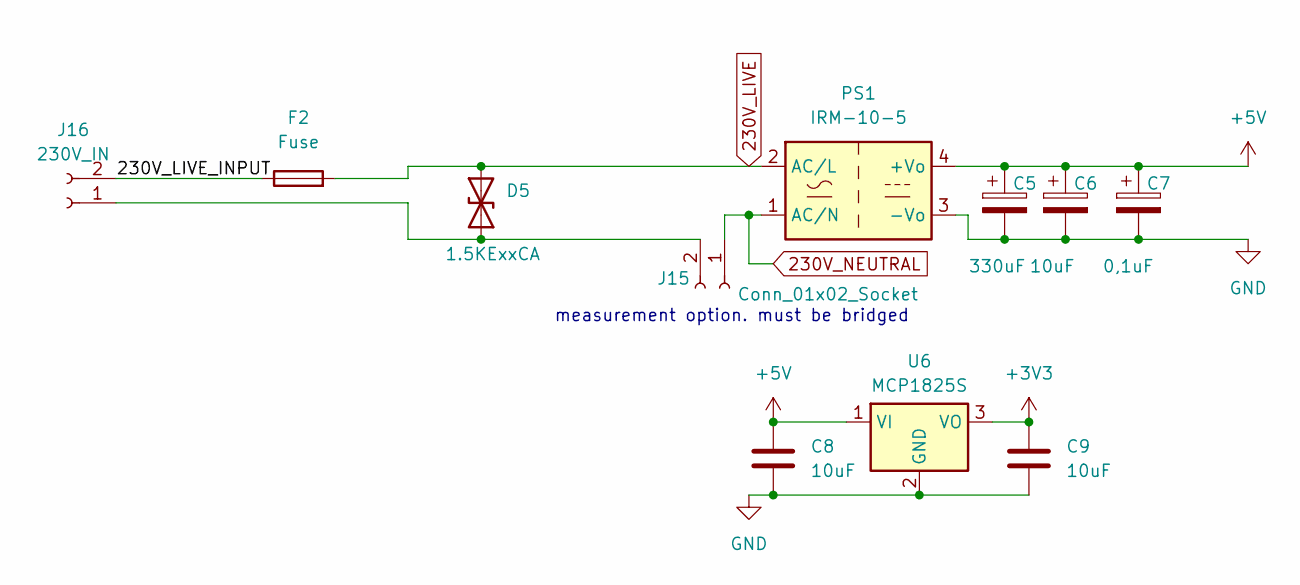
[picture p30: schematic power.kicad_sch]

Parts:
C5: 330uF; CP_Radial_D8.0mm_P5.00mm
C6: 10uF; CP_Radial_D7.5mm_P2.50mm
C7: 0,1uF; CP_Radial_D6.3mm_P2.50mm
C8, C9: 10uF; C_Disc_D3.0mm_W2.0mm_P2.50mm
D5: 1.5KExxCA; D_DO-201AE_P15.24mm_Horizontal
F2: Fuse; Fuseholder_Clip-5x20mm_Keystone_3512_Inline_P23.62x7.27mm_D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
J15: Conn_01x02_Socket; TerminalBlock_bornier-2_P5.08mm
J16: 230V_IN; TerminalBlock_bornier-2_P5.08mm
PS1: IRM-10-5; Converter_ACDC_MeanWell_IRM-10-xx_THT
U6: MCP1825S; SOT-223-3_TabPin2

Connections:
230V_LIVE: D5.2 (A2), F2.2, PS1.2 (AC/L); also elsewhere on the board
230V_NEUTRAL: J15.1, PS1.1 (AC/N); also elsewhere on the board
+3V3: C9.1, U6.3 (VO); also elsewhere on the board
+5V: C5.1, C6.1, C7.1, C8.1, PS1.4 (+Vo), U6.1 (VI); also elsewhere on the board
/power conversion/230V_LIVE_INPUT: F2.1, J16.2
GND: C5.2, C6.2, C7.2, C8.2, C9.2, PS1.3 (-Vo), U6.2 (GND); also elsewhere on the board
unnamed: D5.1 (A1), J15.2, J16.1

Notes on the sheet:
measurement option. must be bridged

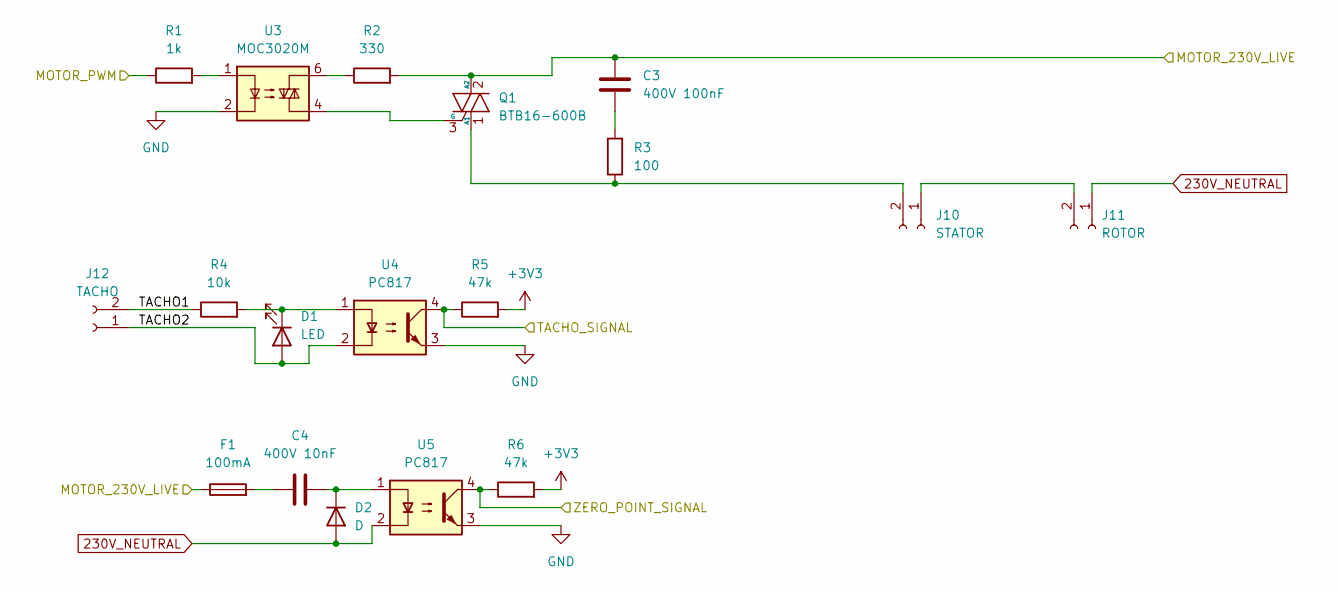
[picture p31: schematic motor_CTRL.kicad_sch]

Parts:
C3: 400V 100nF; C_Disc_D7.0mm_W2.5mm_P5.00mm
C4: 400V 10nF; C_Disc_D7.0mm_W2.5mm_P5.00mm
D1: LED; LED_D5.0mm
D2: D; D_T-1_P5.08mm_Horizontal
F1: 100mA; Fuseholder_Clip-5x20mm_Keystone_3512_Inline_P23.62x7.27mm_D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
J10: STATOR; TerminalBlock_bornier-2_P5.08mm
J11: ROTOR; TerminalBlock_bornier-2_P5.08mm
J12: TACHO; TerminalBlock_bornier-2_P5.08mm
Q1: BTB16-600B; TO-220-3_Vertical
R1: 1k; R_Axial_DIN0204_L3.6mm_D1.6mm_P7.62mm_Horizontal
R2: 330; R_Axial_DIN0204_L3.6mm_D1.6mm_P7.62mm_Horizontal
R3: 100; R_Axial_DIN0204_L3.6mm_D1.6mm_P7.62mm_Horizontal
R4: 10k; R_Axial_DIN0204_L3.6mm_D1.6mm_P7.62mm_Horizontal
R5, R6: 47k; R_Axial_DIN0204_L3.6mm_D1.6mm_P7.62mm_Horizontal
U3: MOC3020M; DIP-6_W7.62mm
U4, U5: PC817; DIP-4_W7.62mm

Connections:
230V_NEUTRAL: D2.2 (A), J11.1, U5.2; also elsewhere on the board
+3V3: R5.2, R6.2; also elsewhere on the board
/MCU/2: R6.1, U5.4; also elsewhere on the board
/MCU/15: R5.1, U4.4; also elsewhere on the board
/Motor control/MOTOR_230V_LIVE: C3.2, F1.1, Q1.2 (A2), R2.2; also elsewhere on the board
/Motor control/MOTOR_PWM: R1.1; also elsewhere on the board
/Motor control/TACHO1: J12.2, R4.1
/Motor control/TACHO2: D1.2 (A), J12.1, U4.2
GND: U3.2, U4.3, U5.3; also elsewhere on the board
unnamed: C3.1, R3.2
unnamed: C4.1, F1.2
unnamed: D1.1 (K), R4.2, U4.1
unnamed: C4.2, D2.1 (K), U5.1
unnamed: J10.1, J11.2
unnamed: J10.2, Q1.1 (A1), R3.1
unnamed: Q1.3 (G), U3.4
unnamed: R1.2, U3.1
unnamed: R2.1, U3.6

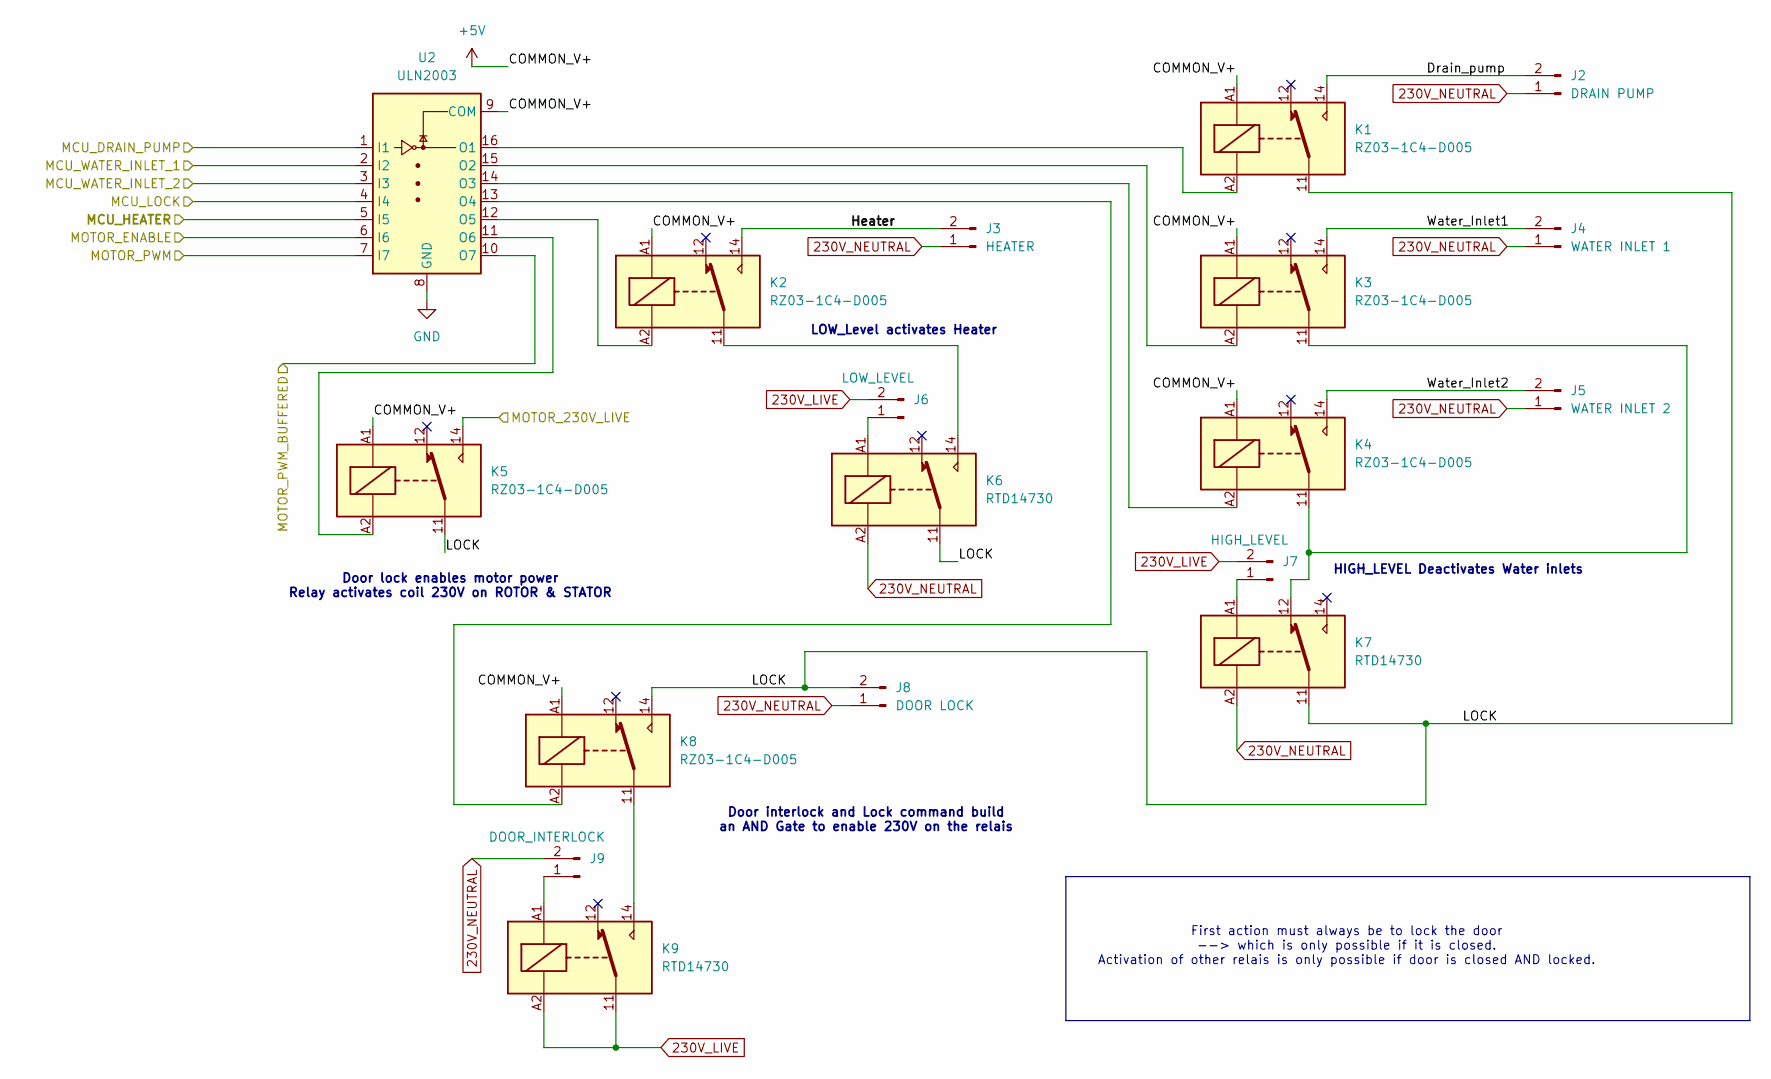
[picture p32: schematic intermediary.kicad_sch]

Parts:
J2: DRAIN PUMP; TerminalBlock_bornier-2_P5.08mm
J3: HEATER; TerminalBlock_bornier-2_P5.08mm
J4: WATER INLET 1; TerminalBlock_bornier-2_P5.08mm
J5: WATER INLET 2; TerminalBlock_bornier-2_P5.08mm
J6: LOW_LEVEL; TerminalBlock_bornier-2_P5.08mm
J7: HIGH_LEVEL; TerminalBlock_bornier-2_P5.08mm
J8: DOOR LOCK; TerminalBlock_bornier-2_P5.08mm
J9: DOOR_INTERLOCK; TerminalBlock_bornier-2_P5.08mm
K1, K2, K3, K4, K5, K8: RZ03-1C4-D005; Relay_SPDT_Schrack-RT1-16A-FormC_RM5mm
K6, K7, K9: RTD14730; Relay_SPDT_Schrack-RT1-16A-FormC_RM5mm
U2: ULN2003; SOIC-16_3.9x9.9mm_P1.27mm

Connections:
230V_LIVE: J6.2, J7.2, K9.11, K9.A2; also elsewhere on the board
230V_NEUTRAL: J2.1, J3.1, J4.1, J5.1, J8.1, J9.2, K6.A2, K7.A2; also elsewhere on the board
+5V: K1.A1, K2.A1, K3.A1, K4.A1, K5.A1, K8.A1, U2.9 (COM); also elsewhere on the board
/MCU/0: U2.5 (I5); also elsewhere on the board
/MCU/10: U2.4 (I4); also elsewhere on the board
/MCU/11: U2.1 (I1); also elsewhere on the board
/MCU/12: U2.3 (I3); also elsewhere on the board
/MCU/13: U2.2 (I2); also elsewhere on the board
/MCU/14: U2.6 (I6); also elsewhere on the board
/MCU/16: U2.7 (I7); also elsewhere on the board
/Motor control/MOTOR_230V_LIVE: K5.14; also elsewhere on the board
/Motor control/MOTOR_PWM: U2.10 (O7); also elsewhere on the board
/intermediary/Drain_pump: J2.2, K1.14
/intermediary/Heater: J3.2, K2.14
/intermediary/LOCK: J8.2, K1.11, K5.11, K6.11, K7.11, K8.14
/intermediary/Water_Inlet1: J4.2, K3.14
/intermediary/Water_Inlet2: J5.2, K4.14
GND: U2.8 (GND); also elsewhere on the board
unnamed: J6.1, K6.A1
unnamed: J7.1, K7.A1
unnamed: J9.1, K9.A1
unnamed: K2.11, K6.14
unnamed: K3.11, K4.11, K7.12
unnamed: K8.11, K9.14
unnamed: K1.A2, U2.16 (O1)
unnamed: K3.A2, U2.15 (O2)
unnamed: K4.A2, U2.14 (O3)
unnamed: K8.A2, U2.13 (O4)
unnamed: K2.A2, U2.12 (O5)
unnamed: K5.A2, U2.11 (O6)

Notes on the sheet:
Door lock enables motor power Relay activates coil 230V on ROTOR & STATOR
HIGH_LEVEL Deactivates Water inlets
Door interlock and Lock command build an AND Gate to enable 230V on the relais
LOW_Level activates Heater
First action must always be to lock the door --> which is only possible if it is closed. Activation of other relais is only possible if door is closed AND locked.

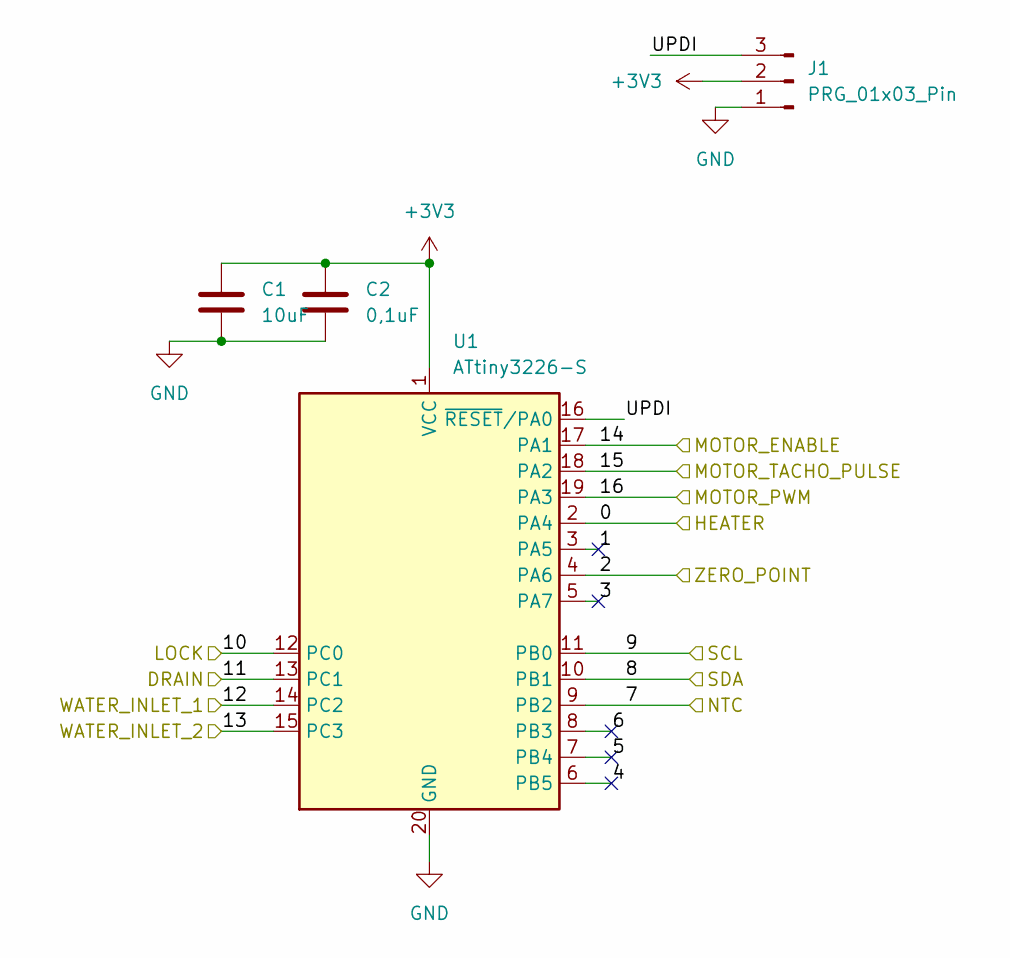
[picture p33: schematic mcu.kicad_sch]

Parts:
C1: 10uF; C_Disc_D3.0mm_W1.6mm_P2.50mm
C2: 0,1uF; C_Disc_D3.0mm_W1.6mm_P2.50mm
J1: PRG_01x03_Pin; PinHeader_1x03_P2.54mm_Vertical
U1: ATtiny3226-S; SOIC-20W_7.5x12.8mm_P1.27mm

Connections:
+3V3: C1.1, C2.1, J1.2, U1.1 (VCC); also elsewhere on the board
/MCU/0: U1.2 (PA4); also elsewhere on the board
/MCU/1: U1.3 (PA5)
/MCU/2: U1.4 (PA6); also elsewhere on the board
/MCU/3: U1.5 (PA7)
/MCU/4: U1.6 (PB5)
/MCU/5: U1.7 (PB4)
/MCU/6: U1.8 (PB3)
/MCU/7: U1.9 (PB2); also elsewhere on the board
/MCU/8: U1.10 (PB1); also elsewhere on the board
/MCU/9: U1.11 (PB0); also elsewhere on the board
/MCU/10: U1.12 (PC0); also elsewhere on the board
/MCU/11: U1.13 (PC1); also elsewhere on the board
/MCU/12: U1.14 (PC2); also elsewhere on the board
/MCU/13: U1.15 (PC3); also elsewhere on the board
/MCU/14: U1.17 (PA1); also elsewhere on the board
/MCU/15: U1.18 (PA2); also elsewhere on the board
/MCU/16: U1.19 (PA3); also elsewhere on the board
/MCU/UPDI: J1.3, U1.16 (~RESET/PA0)
GND: C1.2, C2.2, J1.1, U1.20 (GND); also elsewhere on the board

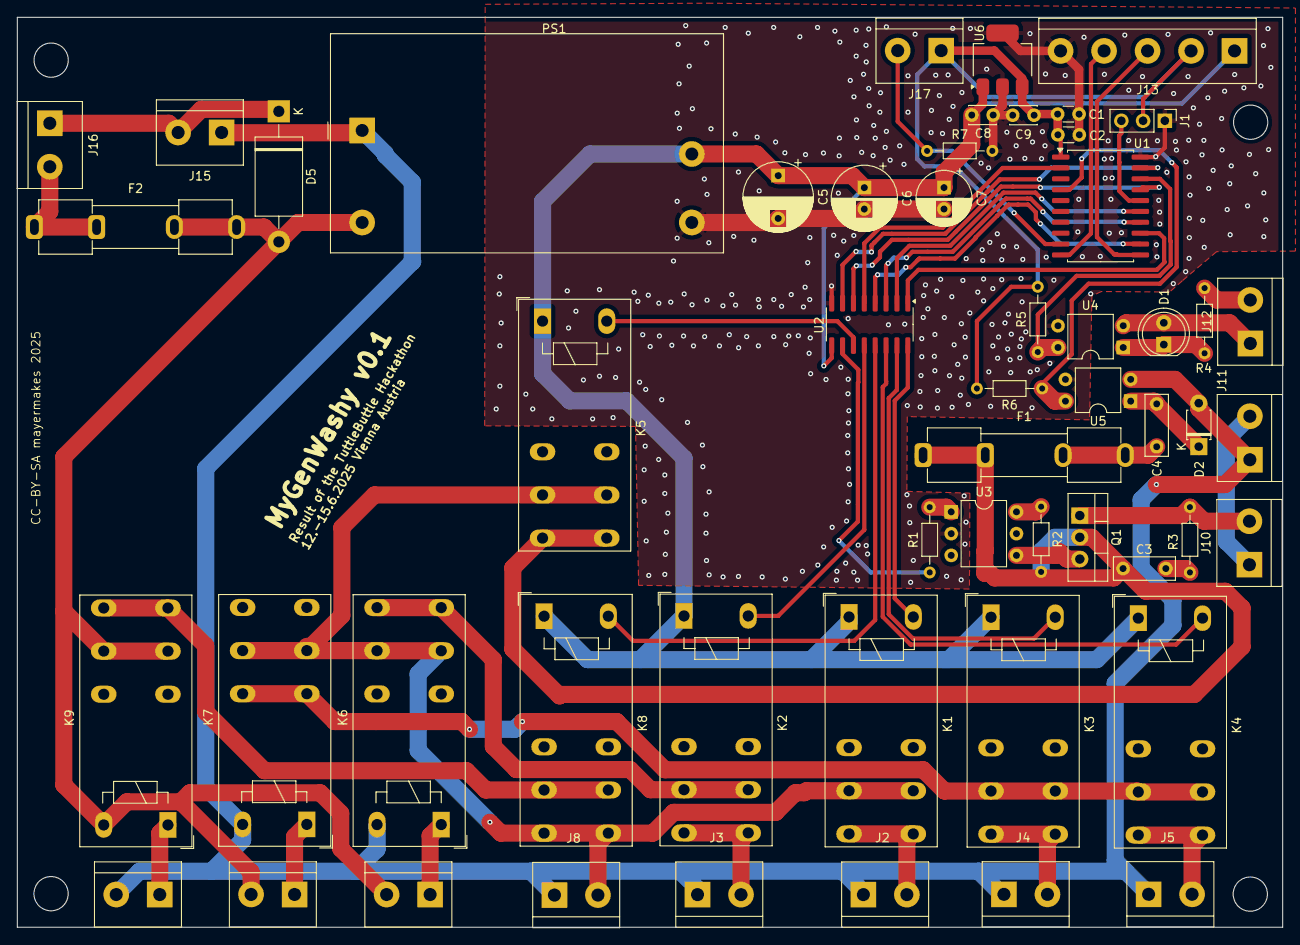
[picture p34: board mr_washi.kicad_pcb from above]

Board: 2 copper layers, 147.8 x 106.3 mm, 54 parts (0 on the bottom side), 50 nets.

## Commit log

2025-06-15 initial upload
    Untested Board, direct result on Sunday 22:30
    [intermediary.kicad_sch, mcu.kicad_sch, motor_CTRL.kicad_sch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]
2025-06-17 Add BOM
    [bom.csv]
2025-06-19 updated new revision
    rotated one relay, better separation of AC and 5V line,
    [mr_washi.kicad_pcb]
2025-06-25 BOM sourceable via Farnell
    Bom to build our First DEV units.
    High Quality parts from Farnell.com
    amounts to build 2 units + spares.
    [MyGenWashi_BOM_Farnell.csv]

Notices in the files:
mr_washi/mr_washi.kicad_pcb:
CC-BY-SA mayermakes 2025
